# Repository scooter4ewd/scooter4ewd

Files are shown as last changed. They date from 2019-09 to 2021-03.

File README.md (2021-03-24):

# Scooter4EWD 
**Scooter 4 electric wheel drive** - электрическое транспортного средства с четырьмя мотор колесами, на одну персону, созданное из доступных материалов.

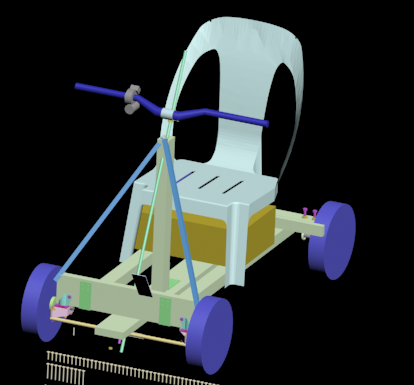
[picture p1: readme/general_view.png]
Общий вид


## Перед началом
Все ниже описанное является собственным опытом и должно расцениваться как хобби, при попытке повторить вы должны оценить как материальные затраты > 30 000 рублей, так и временные ресурсы.

## Список деталей

| №  | Деталь | шт | Цена | Сумма |
| --- | --- | ---| --- | --- |
| [1](readme/part/01/01part.md) | [Колесо гироскутера](readme/part/01/01part.md) | 4 | | 15000 (цена за 2 гироскутера) |
| [2](readme/part/02/02part.md) | [Брус 25х100х1250 (центральный лонжерон)](readme/part/02/02part.md) | 1 | | 100 |
| [3](readme/part/03/03part.md) | [Брус 25х100х500 (передняя ось)](readme/part/03/03part.md) | 1 | | |
| [4](readme/part/04/04part.md) | [Брус 40х50х960 (боковой лонжерон)](readme/part/04/04part.md) | 2 | | 150 |
| [5](readme/part/05/05part.md) | [Брус 40х50х480 (задняя ось)](readme/part/05/05part.md) | 1 | | |
| [6](readme/part/06/06part.md) | [Брус 40х50х407 (стойка рулевой колонки)](readme/part/06/06part.md) | 1 | | |
| [8](readme/part/08/08part.md) | [Уголок 40х40](readme/part/08/08part.md) | 2 | 10 | 20 |
| [9](readme/part/09/09part.md) | [Уголок 40х95](readme/part/09/09part.md) | 3 | 20 | 60 |
| [10](readme/part/10/10part.md) | [Пластина 35х100](readme/part/10/10part.md)| 4 | 10 | 40 |
| [11](readme/part/11/11part.md) | [Рым гайка м8](readme/part/11/11part.md)| 4 | 70 | 280 |
| [12](readme/part/12/12part.md) | [Болт м8х80](readme/part/12/12part.md)| 4 | 15 | 60 |
| [13](readme/part/13/13part.md) | [Болт м8х50](readme/part/13/13part.md)| 1 | 10 | 10 |
| [14](readme/part/14/14part.md) | [Гайка м8х24](readme/part/14/14part.md)| 1 | 30 | 30 |
| [15](readme/part/15/15part.md) | [Гайка м8](readme/part/15/15part.md)| 5 | 10 | 50 |
| [16](readme/part/16/16part.md) | [Шайба м8](readme/part/16/16part.md)| 4 | 5 | 20 |
| [17](readme/part/17/17part.md) | [Болт м6х40](readme/part/17/17part.md)| 10 | 10 | 100 |
| [18](readme/part/18/18part.md) | [Гайка м6](readme/part/18/18part.md)| 11 | | 50 |
| [19](readme/part/19/19part.md) | [Шайба м6](readme/part/19/19part.md)| 8 | | 40 |
| [20](readme/part/20/20part.md) | [Колесо мебельное 43х58 d40](readme/part/20/20part.md)| 2 | | 300 |
| [21](readme/part/21/21part.md) | [Болт м5х50](readme/part/21/21part.md)| 2 | | 30 |
| [22](readme/part/22/22part.md) | [Гайка м5](readme/part/22/22part.md)| 4 | | 20 |
| [23](readme/part/23/23part.md) | [Шайба м5](readme/part/23/23part.md)| 2 | | 10 |
| [24](readme/part/24/24part.md) | [Ось руля 20х20х1000](readme/part/24/24part.md)| 1 | | 75 |
| [27](readme/part/27/27part.md) | [Трубка алюминиевая d12х480](readme/part/27/27part.md)| 1 | | 50 |
| [28](readme/part/28part.md) | [Пластина 25х60](readme/part/28part.md)| 1 | | 20 |
| [29](readme/part/29/29part.md) | [Вынос руля](readme/part/29/29part.md)| 1 | | 25 |
| [30](readme/part/30/30part.md) | [Уголок алюминиевый 15х580](readme/part/30/30part.md)| 2 | | 100 |
| [31](readme/part/31part.md) | [Стул пластмассовый](readme/part/31part.md)| 1 | | 300 |
| [32](readme/part/32/32part.md) | [Руль велосипедный](readme/part/32/32part.md)| 1 | | 600 |
| [33](readme/part/33part.md) | [Ручка газа](readme/part/33part.md)| 1 | | 460 |
| [34](readme/part/34/34part.md) | [Саморез 25](readme/part/34/34part.md)| 59 | | 100 |
| [35](readme/part/35/35part.md) | [Саморез 50](readme/part/35/35part.md)| 10 | | 20 |
| [36](readme/part/36/36part.md) | [Стяжка 3х200](readme/part/36/36part.md)| 17 | | 150 |
| [38](readme/part/38/38part.md) | [Чемодан](readme/part/38/38part.md)| 1 | | 1500 |
| [39](readme/part/39/39part.md) | [Разъем DHS-78](readme/part/39/39part.md)| 1 | | 400 |
| [40](readme/part/40part.md) | [Провод силовой](readme/part/40part.md)| 10 | | 500 |
| [41](readme/part/41part.md) | [Витая пара](readme/part/41part.md)| 10 | | 200 |
| [42](readme/part/42part.md) | [Рукав металлический](readme/part/42part.md)| 1 | | 50 |
| [43](readme/part/43part.md) | [Клеммная колодка](readme/part/43part.md)| 4 | | 50 |
| [52](readme/part/52/52part.md) | [Поворотный механизм - кулак левый](readme/part/52/52part.md)| 1 | | 300 |
| [53](readme/part/53/53part.md) | [Поворотный механизм - кулак правый](readme/part/53/53part.md)| 1 | | 300 |
| [54](readme/part/54/54part.md) | [Втулка оси руля (низ)](readme/part/54/54part.md)| 1 | | 300 |
| [55](readme/part/55/55part.md) | [Подшипник руля (болт)](readme/part/55/55part.md)| 2 | | 300 |
| [56](readme/part/56/56part.md) | [Подшипник руля (гайка)](readme/part/56/56part.md)| 2 | | 300 |
| [57](readme/part/57/57part.md) | [Втулка оси руля (верх)](readme/part/57/57part.md)| 1 | | 300 |
| [58](readme/part/58part.md) | [Аккумулятор](readme/part/58part.md)| 2 | 1950 | 3900 |
| [59](readme/part/59part.md) | [Контроллер электродвигателя 350wt](readme/part/59part.md)| 4 | 600 | 2400 |
| [60](readme/part/60part.md) | [Зарядное устройство от гироскутера](readme/part/60part.md)| 1 | | |
| [61](readme/part/61part.md) | [Автомат защиты](readme/part/61part.md)| 2 | 150 | 300 |
| [62](readme/part/62part.md) | [Ваттметр](readme/part/62part.md)| 1 | 700 | 700 |
| [63](readme/part/63part.md) | [Кнопка заднего хода](readme/part/63part.md)| 1 | 70 | 70 |
| [64](readme/part/64part.md) | [Кнопка нажатия тормоза](readme/part/64part.md)| 1 | 50 | 50 |
| [65](readme/part/65part.md) | [Блок кнопок на руль](readme/part/65part.md)| 1 | 200 | 200 |
| [66](readme/part/66part.md) | [Грипсы](readme/part/66part.md)| 2 | | 300 |
| [67](readme/part/67/67part.md) | [Ротор дискового тормоза](readme/part/67/67part.md)| 2 | | |
| [68](readme/part/68part.md) | [Суппорт дискового тормоза](readme/part/68part.md)| 2 | | 2500 |
| [69](readme/part/69part.md) | [Гидролиния](readme/part/69part.md)| 2 | | |
| [70](readme/part/70part.md) | [Ручка тормоза](readme/part/70part.md)| 2 | | |
| [71](readme/part/71/71part.md) | [Проставка для ротора дискового тормоза](readme/part/71/71part.md)| 2 | | 300 |
| [72](readme/part/72part.md) | [Тумблер](readme/part/72part.md)| 8 | | 400 |
| [73](readme/part/73part.md) | [Разъем XT60 папа](readme/part/73part.md)| 8 | | 400 |
| [74](readme/part/74part.md) | [Консоль включения аккумуляторов](readme/part/74part.md)| 1 | | |
| [75](readme/part/75part.md) | [Крепление суппорта дискового тормоза](readme/part/75part.md)| 2 | | 100 |
| [76](readme/part/76part.md) | [Тяга рулевого управления](readme/part/76part.md)| 2 | | 1000 |
| | | | **итого** | **35390** |

## Как строить
1. Брус 25х100 нарезать по длине на 1250мм и 500мм, получаем детали центральный лонжерон ([№2](readme/part/02/02part.md)), 
передняя ось ([№3](readme/part/03/03part.md)).
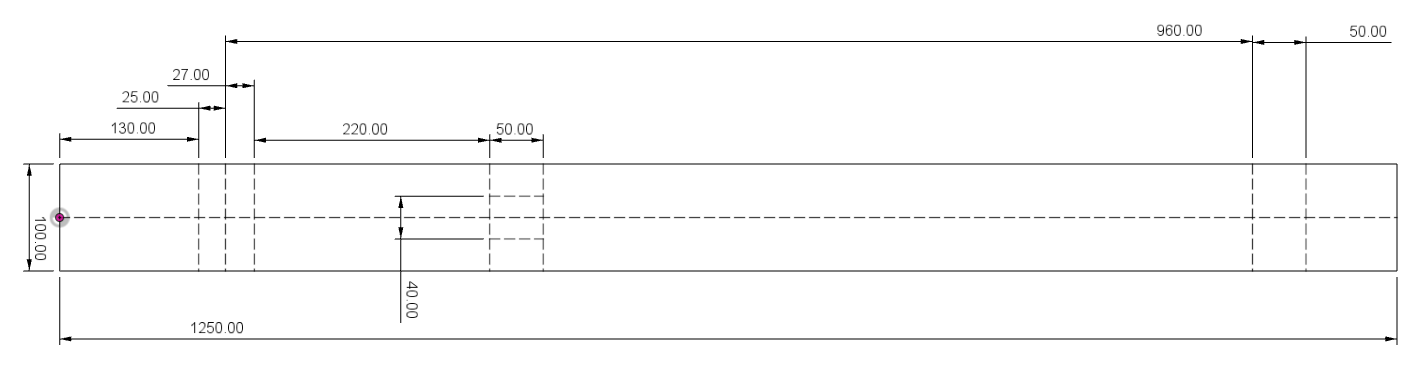
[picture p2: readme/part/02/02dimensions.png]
1. Наносим разметку на центральный лонжерон ([№2](readme/part/02/02part.md)). 
   1. Линию вдоль доски - центральную ось (50мм от бока).
   1. Место крепления передней оси ([№3](readme/part/03/03part.md)): перпендикулярная линия 130мм от края и 
   еще одну через 25мм (155мм от края).
   1. Место крепления стойки руля ([№6](readme/part/06/06part.md)): перпендикулярная линия 375мм от края, 
   еще одну через 50мм (425мм от края), 
   нарисовать прямоугольник 50х40мм на основе полученных ранее линий и по центру по ширине (20мм от оси).
   1. Место крепления задней оси ([№5](readme/part/05/05part.md)): перпендикулярная линия 1115мм от края, 
   еще одну через 50мм (1165мм от края). 
1. Просверлить отверстие для руля ([№24](readme/part/24/24part.md)), диаметр 30мм, на расстоянии 27мм от передней оси (182мм от края), отверстие должно идти под углом 22,5° (его можно получить если из листа А4 вырезать прямоугольный треугольник со сторонами 297мм на 123мм).
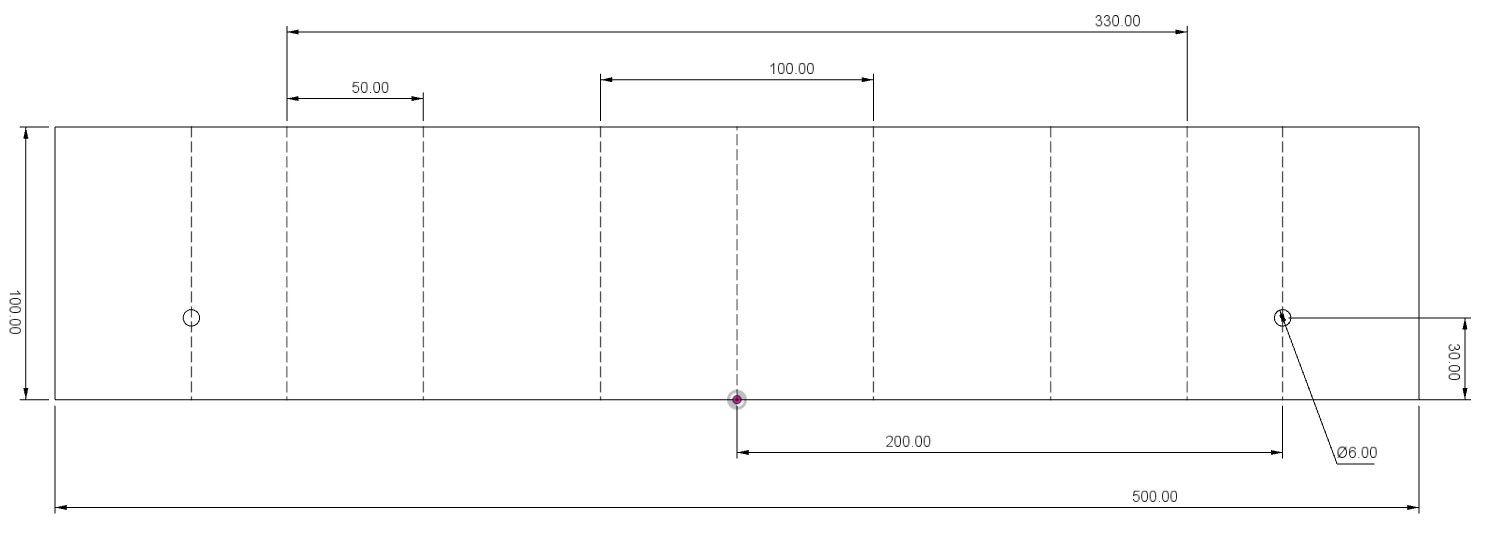
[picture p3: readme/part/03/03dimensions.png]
1. Наносим разметку на переднюю ось ([№3](readme/part/03/03part.md)). 
   1. Линию оси (250мм от края).
   1. Линии центрального лонжерона 50мм в обе стороны от ось.
   1. Линии боковых лонжеронов 115мм и 165мм по обе стороны от ось.
   1. Линии крепления передних колес 200мм по обе стороны от ось.
   1. Центр отверстия крепления механизма вращения передних колес, на линии из предыдущего пункта на расстоянии 30мм от бока.
1. Просверлить отверстия диаметром 6мм для крепления механизма вращения передних колес ([№20](readme/part/20/20part.md)
1. Брус 40х50 нарезать по длине на 960мм два штуки, 480мм, 407мм, получаем детали боковые лонжероны ([№4](readme/part/04/04part.md)), 
задняя ось ([№5](readme/part/05/05part.md)), стойка рулевой колонки ([№6](readme/part/06/06part.md)))
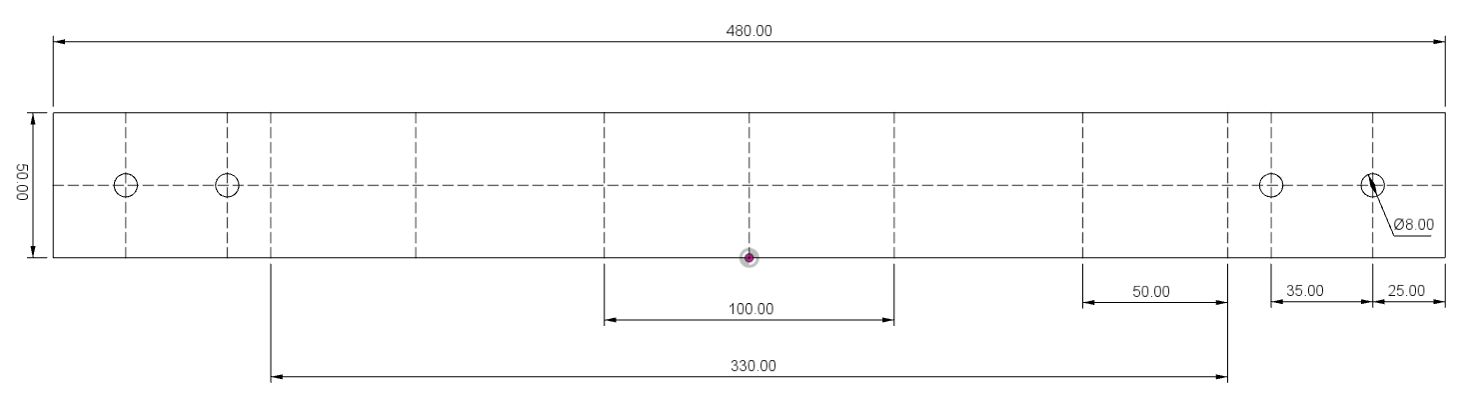
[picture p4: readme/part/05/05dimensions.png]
1. Наносим разметку на заднюю ось ([№5](readme/part/05/05part.md)) 
   1. Линию оси вдоль (25мм от бока).
   1. Линию оси по ширите (240мм от края).
   1. Линии центрального лонжерона 50мм в обе стороны от ось.
   1. Линии боковых лонжеронов 115мм и 165мм по обе стороны от ось.
   1. Линии крепления задних колес 25мм и 60мм по обе стороны от края.
1. Просверлить отверстия диаметром 8мм для крепления задних колес.
1. Собираем основу рамы, на ровной поверхности выкладываем прямоугольник из передней оси ([№3](readme/part/03/03part.md)), 
лонжероны 2 шт ([№4](readme/part/04/04part.md)), задняя ось ([№5](readme/part/05/05part.md)), проверяем что углы прямые
1. Полученный прямоугольник соединяем, заднюю ось ([№5](readme/part/05/05part.md)) уголками ([№8](readme/part/08big.md) по внутреннему периметру двенадцатью саморезами ([№34](readme/part/34/34part.md)),
1. Переднюю ось ([№3](readme/part/03/03part.md)) уголком ([№9](readme/part/09/09part.md)). 
Уголок необходимо подложить под раму, сначала крепим уголок к передней оси восьмью саморезами ([№34](readme/part/34/34part.md)), 
затем подымаем раму и фиксируем уголки на боковых лонжеронах 8 саморезами ([№35](readme/part/35/35part.md)).
1. Усиливаем крепление задней оси прикручивая пластина 35х100 ([№10](readme/part/10/10part.md)) 12 саморезами ([№34](readme/part/34/34part.md))
1. Выставляем по центру лонжерон ([№2](readme/part/02/02part.md)), прикручиваем 6 саморезами ([№35](readme/part/35/35part.md)), 
три к передней оси ([№3](readme/part/03/03part.md)), три к задней оси ([№5](readme/part/05/05part.md)) 
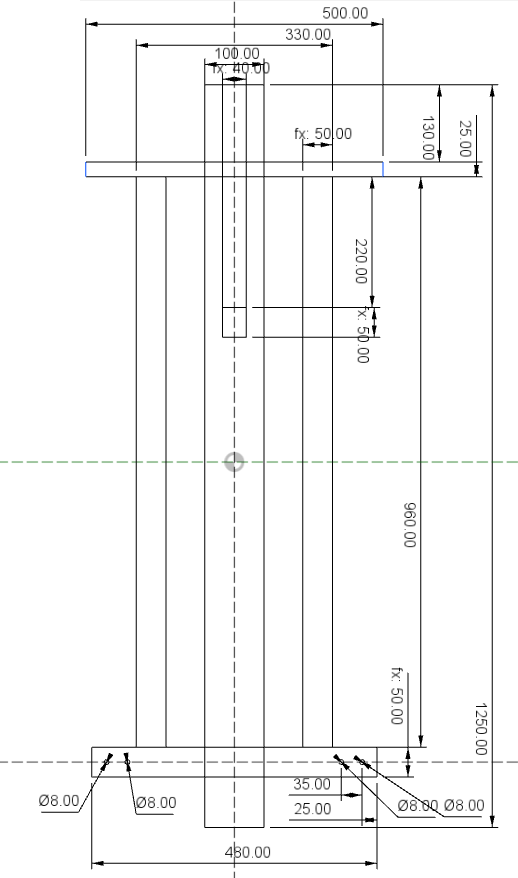
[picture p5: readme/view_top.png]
Общий чертёж

1. На четыре болта ([№12](readme/part/12/12part.md)) накрутить четыре гайки (№15) и надеть четыре шайбы ([№16](readme/part/16/16part.md).
1. Болты ([№12](readme/part/12/12part.md)) вставить в заднюю ось ([№5](readme/part/05/05part.md)), 
наживить рым гайками ([№11](readme/part/11/11part.md)). 
1. Пара рым гайками ([№11](readme/part/11/11part.md)) с одной стороны должна держать ось колеса ([№1](readme/part/01/01part.md)).
   1. Прижать ось колеса ([№1](readme/part/01/01part.md)) болтом ([№12](readme/part/12/12part.md)).
   1. Зафиксировать болт ([№12](readme/part/12/12part.md)) на оси подтянув гайку ([№11](readme/part/11/11part.md)).
1. Необходимо добиться параллельности оси колес ([№1](readme/part/01/01part.md)) к задней оси ([№5](readme/part/05/05part.md)). 
Проверить под нагрузкой - стать на заднюю ось ([№5](readme/part/05/05part.md)). 
В случае необходимости, рым гайками ([№11](readme/part/11/11part.md)), можно подпилить напильником.
1. Мебельное колесо ([№20](readme/part/20/20part.md)) разобрать, вынуть колесо.
1. Мебельное колесо ([№20](readme/part/20/20part.md)) крепим к передней оси за ухо в котором было колесико.
1. В поворотный кулак ([№52](readme/part/52/52part.md)) вставить ось колеса ([№1](readme/part/01/01part.md)).
1. Поворотный кулак ([№52](readme/part/52/52part.md)) вместе с колесом ([№1](readme/part/01/01part.md)) 
крепим к площадке мебельного колеса ([№20](readme/part/20/20part.md)) четырьмя болтами ([№17](readme/part/17/17part.md)), 
подкладываем шайбы  ([№19](readme/part/19/19part.md)), закручиваем гайку ([№18](readme/part/18/18part.md))
1. Аналогично с другой стороны для ([№53](readme/part/53/53part.md))
1. Поворотные кулаки ([№52](readme/part/52/52part.md), [№53](readme/part/53/53part.md)) между собой соединяем трубкой ([№27](readme/part/27/27part.md)).
Для этого нам понадобится два болта ([№21](readme/part/21/21part.md)), две шайбы ([№23](readme/part/21/21part.md)) и шесть гаек ([№22](readme/part/22/22part.md))
   1. В трубке ([№27](readme/part/27/27part.md)) просверлить отверстие диаметром 5мм в 5мм от края. Расстояние между отверстиями должно составлять 480мм.
   1. Болт ([№21](readme/part/21/21part.md)) продеть в отверстие в трубке ([№27](readme/part/27/27part.md)).
   1. Наживить гайку ([№22](readme/part/22/22part.md)) вплотную к трубке ([№27](readme/part/27/27part.md)).
   1. Смазать болт ([№21](readme/part/21/21part.md)), можно использовать обычное мыло, этого будет достаточно.
   1. Болт ([№21](readme/part/21/21part.md)) вкрутить в поворотный кулак ([№52](readme/part/52/52part.md)).
   1. Затянуть гайку ([№22](readme/part/22/22part.md)) зафиксировав болт ([№21](readme/part/21/21part.md)) на трубке.
   1. Надеть шайбу ([№23](readme/part/21/21part.md)).
   1. Наживить гайку ([№22](readme/part/22/22part.md)) вплотную к шайбе ([№23](readme/part/21/21part.md)).
   1. Наживить еще одну гайку ([№22](readme/part/22/22part.md)) вплотную к предыдущей.
   1. Затянуть гайки между собой, болт ([№21](readme/part/21/21part.md)) должен свободно вращаться в кулаке ([№52](readme/part/52/52part.md)).
1. Повторить процедуру с другой стороны
1. К стойку руля ([№6](readme/part/06/06part.md)) к краю крепим уголок ([№9](readme/part/09/09part.md)) на четыре самореза ([№34](readme/part/34/34part.md))
1. Вторую площадку уголка ([№9](readme/part/09/09part.md)) крепим к центральному лонжерону ([№2](readme/part/02/02part.md)) на четыре самореза ([№34](readme/part/34/34part.md)), 
выставив брус ([№6](readme/part/06/06part.md)) перпендикулярно на размеченный в центре прямоугольник.
1. Нижняя втулка руля ([54](readme/part/54/54part.md)) крепится двумя саморезами ([№35](readme/part/35/35part.md)) к передней оси ([№3](readme/part/03/03part.md))
и двумя саморезами ([№35](readme/part/35/35part.md)) к центральному лонжерону ([№2](readme/part/02/02part.md)).
1. Верхняя втулка руля ([57](readme/part/57/57part.md)) крепится к стойке рулевой колонки ([6](readme/part/06/06part.md)) 
двумя пластинами ([10](readme/part/10/10part.md)) с боков на шестнадцать саморезов ([№34](readme/part/34/34part.md)) 
1. Для увеличение жесткости стойки руля, два уголка ([30](readme/part/30/30part.md)) крепим к верхней втулке руля ([57](readme/part/57/57part.md))
с одной стороны и к краю передней оси ([3](readme/part/03/03part.md)) с другой стороны.
1. TODO Ось руля ([24](readme/part/24/24part.md)) 
1. TODO Вынос руля ([29](readme/part/29/29part.md)), руль ([24](readme/part/24/24part.md))
1. TODO Стул ([31](readme/part/31part.md))
1. TODO Педаль тормоза Петля ввертная ([49](readme/part/49part.md)) Алюминиевый профиль ([50](readme/part/50part.md)) Брус 16х51х150
1. TODO Трос тормоза
1. TODO Уголок крепления блока тормоза
1. TODO Блок тормоза 1
1. TODO Блок тормоза 2
1. TODO Трос
1. TODO Чемодан
1. TODO Аккумулятор
1. TODO Клеммы аккумуляторов
1. TODO Автомат
1. TODO Клеммы питания
1. TODO Контроллеры
1. TODO Клеммы перед разъемом
1. TODO Разъем
1. TODO Клеммы переднего левого колеса
1. TODO Клеммы переднего правого колеса
1. TODO Провода от передних клем до разъема
1. TODO Провода от ручки газа до разъема
1. TODO Клеммы заднего левого колеса
1. TODO Клеммы заднего правого колеса
1. TODO Провода от задних клем до разъема
1. TODO Стяжки изолента

[Распайка разъема](readme/part/39/39part.md)

## Замечания и рекомендации
Мебельные колёса для крепления передних колес необходимо выбирать с запасом прочности и наличием подшипников с двух сторон.

При распайке разъема использовать все пины даже если они не задействованы, 
припаять провод и оставить на нем бирку поможет в дальнейших изменениях (после установки впаять дополнительный провод нереально).

Перед подачей питания, прозвонить каждый провод на обрыв и замыкания между собой.

## Лирика 
Раздел не несет технической информации, но может внести ясность почему так получилось. 
[Читать далее->](readme/history.md)

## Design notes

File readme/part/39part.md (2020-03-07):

# Разем DHS-78

Разем DHS-78

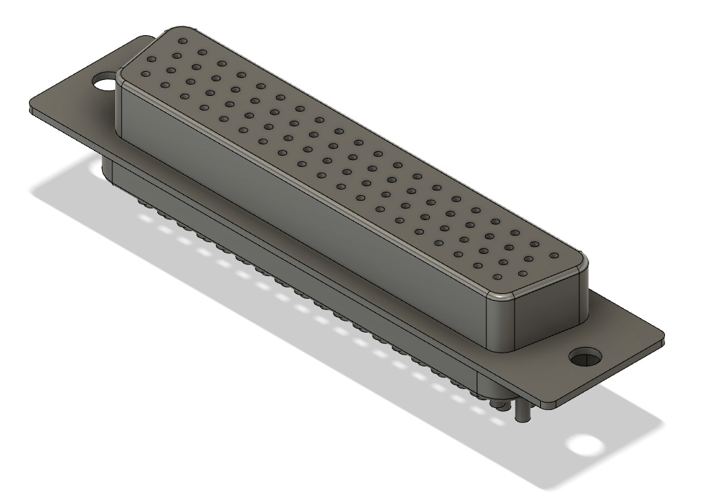
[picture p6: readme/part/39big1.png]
Мама

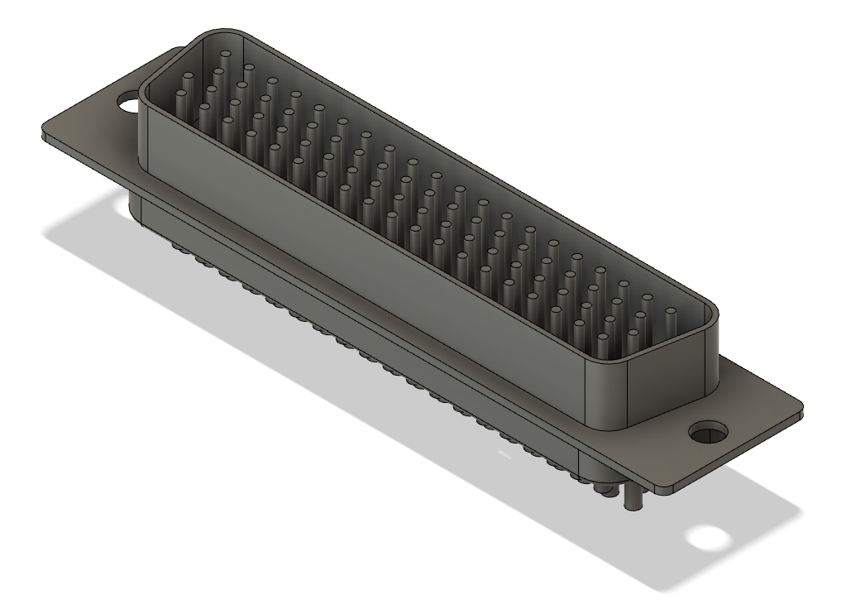
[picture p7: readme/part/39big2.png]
Папа


## Распайка разъема

| № Pin | Ряд | Обозначение | Расшифровка |
| --- | --- | --- | --- |
| 1  | 1 | кппж | колесо передний правый желтый |
| 2  | 1 | кппж |  |
| 3  | 1 | кппз | колесо передний правый зеленый |
| 4  | 1 | кппз |  |
| 5  | 1 | кппс | колесо передний правый синий |
| 6  | 1 | кппс |  |
| 7  | 1 | кплж | колесо передний левый желтый |
| 8  | 1 | кплж |  |
| 9  | 1 | кплз | колесо передний левый зеленый |
| 10 | 1 | кплз |  |
| 11 | 1 | кплс | колесо передний левый синий |
| 12 | 1 | кплс |  |
| 13 | 1 | s+36 | speed +36v (от аккумулятора) |
| 14 | 1 | s вкл | speed вкл. контроллера (замыкается на провод +36v) |
| 15 | 1 | задний ход 1 | задний ход 1 TODO (земля) |
| 16 | 1 | speed | speed уровень газа (+1v .. +4v) |
| 17 | 1 | задний ход 2 | задний ход 2 TODO (замыкается за землю) |
| 18 | 1 | s+5 | speed +5v |
| 19 | 1 | хп+5 | холла передний +5v |
| 20 | 1 | хз+5 | холла задний +5v |
| 21 | 2 | кппж |  |
| 22 | 2 | кппж |  |
| 23 | 2 | кппз |  |
| 24 | 2 | кппз |  |
| 25 | 2 | кппс |  |
| 26 | 2 | кппс |  |
| 27 | 2 | кплж |  |
| 28 | 2 | кплж |  |
| 29 | 2 | кплз |  |
| 30 | 2 | кплз |  |
| 31 | 2 | кплс |  |
| 32 | 2 | кплс |  |
| 33 | 2 | хппж | холла передний правый желтый |
| 34 | 2 | хппз | холла передний правый зеленый |
| 35 | 2 | хппс | холла передний правый синий |
| 36 | 2 | хплж | холла передний левый желтый |
| 37 | 2 | хплз | холла передний левый зеленый |
| 38 | 2 | хплс | холла передний левый синий |
| 39 | 2 |  |  |
| 40 | 3 | кзпж | колесо задний правый желтый |
| 41 | 3 | кзпж |  |
| 42 | 3 | кзпз | колесо задний правый зеленый |
| 43 | 3 | кзпз |  |
| 44 | 3 | кзпс | колесо задний правый синий |
| 45 | 3 | кзпс |  |
| 46 | 3 | кзлж | колесо задний левый желтый |
| 47 | 3 | кзлж |  |
| 48 | 3 | кзлз | колесо задний левый зеленый |
| 49 | 3 | кзлз |  |
| 50 | 3 | кзлс | колесо задний левый синий |
| 51 | 3 | кзлс |  |
| 52 | 3 | хзпж | холла задний правый желтый |
| 53 | 3 | хзпз | холла задний правый зеленый |
| 54 | 3 | хзпс | холла задний правый синий |
| 55 | 3 | хзлж | холла задний левый желтый |
| 56 | 3 | хзлз | холла задний левый зеленый |
| 57 | 3 | хзлс | холла задний левый синий |
| 58 | 3 |  |  |
| 59 | 3 |  |  |
| 60 | 4 | кзпж |  |
| 61 | 4 | кзпж |  |
| 62 | 4 | кзпз |  |
| 63 | 4 | кзпз |  |
| 64 | 4 | кзпс |  |
| 65 | 4 | кзпс |  |
| 66 | 4 | кзлж |  |
| 67 | 4 | кзлж |  |
| 68 | 4 | кзлз |  |
| 69 | 4 | кзлз |  |
| 70 | 4 | кзлс |  |
| 71 | 4 | кзлс |  |
| 72 | 4 |  |  |
| 73 | 4 |  |  |
| 74 | 4 | s- | speed минус (земля) |
| 75 | 4 | хп- | холла передний минус (земля) |
| 76 | 4 | хз- | холла задний минус (земля) |
| 77 | 4 |  |  |
| 78 | 4 |  |  |

Силовые провода к колесам используют по 4 пина, имеют одинаковое обозначение и расположены рядом - два на одном ряду и два на соседнем.

## 3D модели
- [Папа](39_1part.f3d)
- [Мама](39_2part.f3d)

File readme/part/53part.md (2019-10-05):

# Поворотный механизм - кулак правый

Поворотный механизм - кулак правый.
Файлы от левого кулака перед использованием сделать зеркальную копию.

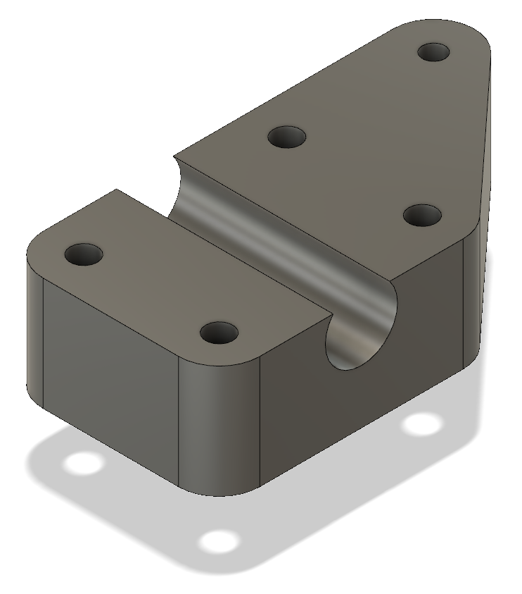
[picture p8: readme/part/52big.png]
Общий вид


[3D модель](52part.f3d)

[Файл для печати на 3D принтере](52part.stl)

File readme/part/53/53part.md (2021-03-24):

# Поворотный механизм - кулак правый

Поворотный механизм - кулак правый.
Файлы от левого кулака перед использованием сделать зеркальную копию.

Общий вид

[3D модель](../52/52part.f3d)

[Файл для печати на 3D принтере](../52/52part.stl)

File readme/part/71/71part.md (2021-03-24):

# Проставка для ротора дискового тормоза

Проставка для ротора дискового тормоза.

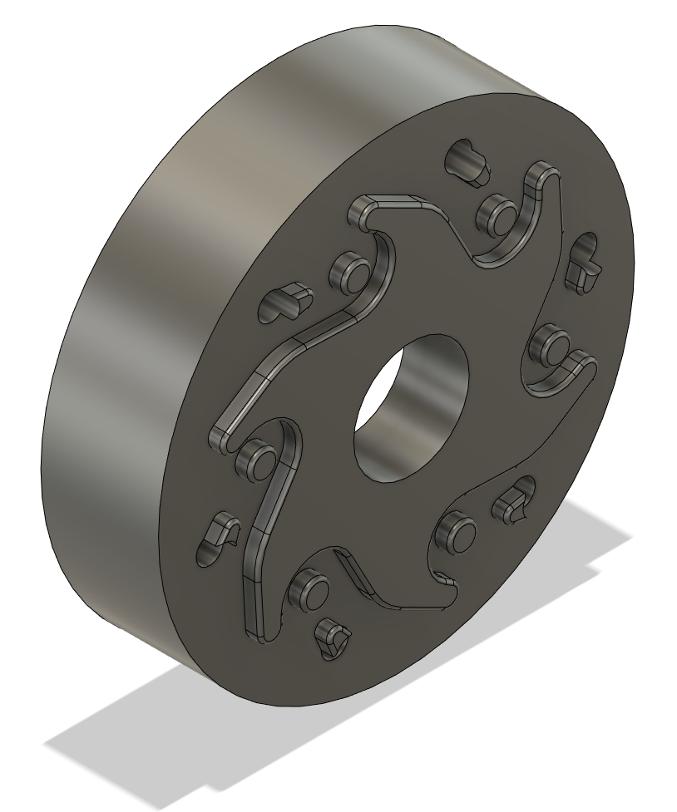
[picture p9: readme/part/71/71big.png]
Общий вид


[3D модель](71part.f3z)

[Файл для печати на 3D принтере](71part.stl)

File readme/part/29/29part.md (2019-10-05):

# Вынос руля

Вынос руля

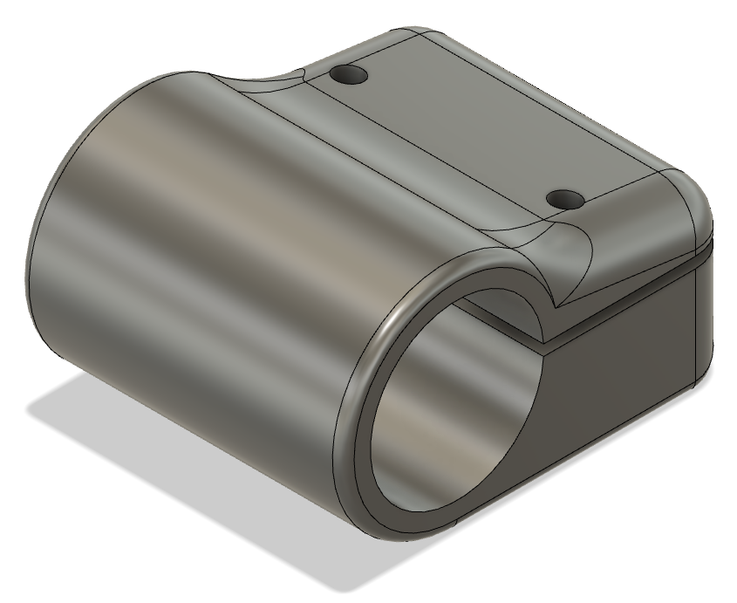
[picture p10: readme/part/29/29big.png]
Общий вид


[3D модель](29part.f3d)

Файл для печати на 3D принтере:
- [Вынос](29part.stl)

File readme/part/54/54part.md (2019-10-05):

# Втулка оси руля низ

Втулка оси руля низ

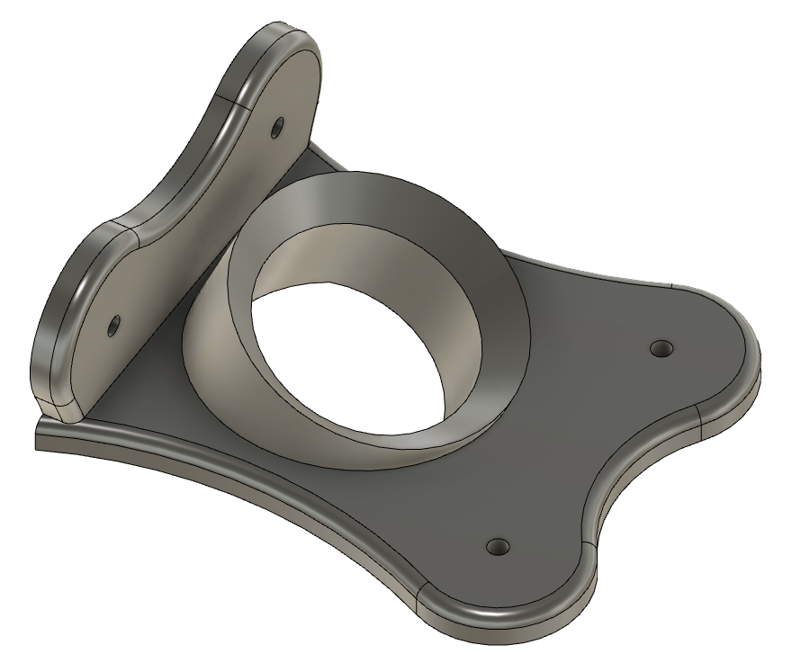
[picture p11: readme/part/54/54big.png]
Общий вид


[3D модель](54part.f3d)

[Файл для печати на 3D принтере](54part.stl)

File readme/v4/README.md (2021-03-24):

# Scooter4EWD 
**Scooter 4 electric wheel drive** - электрическое транспортного средства с четырьмя мотор колесами, на одну персону, созданное из доступных материалов.

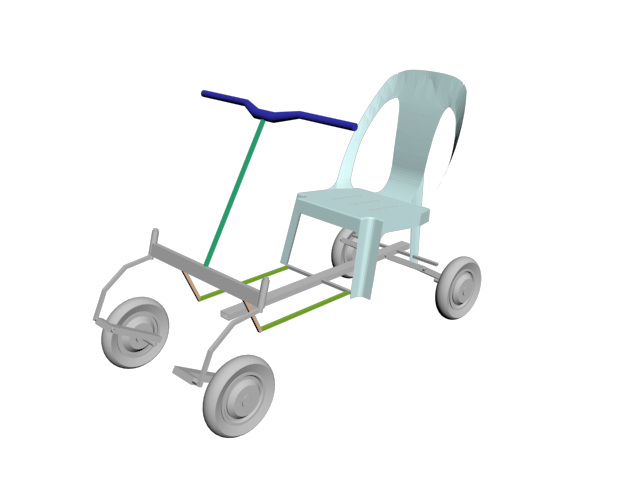
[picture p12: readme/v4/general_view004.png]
Общий вид


## Перед началом
Все ниже описанное является собственным опытом и должно расцениваться как хобби, при попытке повторить вы должны оценить как материальные затраты > 30 000 рублей, так и временные ресурсы.

## Список деталей
TODO

| №  | Деталь | шт | Цена | Сумма |
| --- | --- | ---| --- | --- |
| [1](../part/01/01part.md) | [Колесо гироскутера](../part/02/02part.md) | 4 | | 15000 (цена за 2 гироскутера) |
| [31](../part/31part.md) | [Стул пластмассовый](../part/31part.md)| 1 | | 300 |
| [32](../part/32/32part.md) | [Руль велосипедный](../part/32/32part.md)| 1 | | 600 |
| [33](../part/33part.md) | [Ручка газа](../part/33part.md)| 1 | | 460 |
| [34](../part/34/34part.md) | [Саморез 25](../part/34/34part.md)| | |  |
| [35](../part/35/35part.md) | [Саморез 50](../part/35/35part.md)|  | |  |
| [36](../part/36/36part.md) | [Стяжка 3х200](../part/36/36part.md)|  | |  |
| [38](../part/38/38part.md) | [Чемодан](../part/38/38part.md)| 1 | | 1500 |
| [39](../part/39/39part.md) | [Разъем DHS-78](../part/39/39part.md)| 1 | | 400 |
| [40](../part/40part.md) | [Провод силовой](../part/40part.md)| 10 | | |
| [41](../part/41part.md) | [Витая пара](../part/41part.md)| 10 | | |
| [42](../part/42part.md) | [Рукав металлический](../part/42part.md)| 1 | | 50 |
| [43](../part/43part.md) | [Клеммная колодка](../part/43part.md)| 4 | | 50 |
| [58](../part/58part.md) | [Аккумулятор](../part/58part.md)| 2 | 1950 | 3900 |
| [59](../part/59part.md) | [Контроллер электродвигателя 350wt](../part/59part.md)| 4 | 600 | 2400 |
| [60](../part/60part.md) | [Зарядное устройство от героскутера](../part/60part.md)| 1 | | |
| [61](../part/61part.md) | [Автомат защиты](../part/61part.md)| 1 | 150 | 150 |
| [62](../part/62part.md) | [Ваттметр](../part/62part.md)| 1 | 700 | 700 |
| [63](../part/63part.md) | [Кнопка заднего хода](../part/63part.md)| 1 | 70 | 70 |
| [64](../part/64part.md) | [Кнопка нажатия тормоза](../part/64part.md)| 1 | 50 | 50 |
| [65](../part/65part.md) | [Блок кнопок на руль](../part/65part.md)| 1 | 200 | 200 |
| [66](../part/66part.md) | [Грипсы](../part/66part.md)| 2 | | 300 |
| [67](../part/67/67part.md) | [Ротор дискового тормоза](../part/67/67part.md)| 2 | | |
| [68](../part/68part.md) | [Суппорт дискового тормоза](../part/68part.md)| 2 | | 2500 |
| [69](../part/69part.md) | [Гидролиния](../part/69part.md)| 2 | | |
| [70](../part/70part.md) | [Ручка тормоза](../part/70part.md)| 2 | | |
| [71](../part/71/71part.md) | [Проставка для ротора дискового тормоза](../part/71/71part.md)| 2 | | |
| [72](../part/72part.md) | [Тумблер](../part/72part.md)| 8 | | |
| [73](../part/73part.md) | [Разъем XT60 папа](../part/73part.md)| 8 | | |
| [74](../part/74part.md) | [Консоль включения аккумуляторов](../part/73part.md)| 1 | | |
| | | | **итого** | **** |

## Как строить
1. TODO 

[Распайка разъема](../part/39/39part.md)

## Замечания и рекомендации
TODO

## Лирика 
Раздел не несет технической информации, но может внести ясность почему так получилось. 
[Читать далее->](../history.md)

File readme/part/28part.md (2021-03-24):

# Пластина 25х60

Пластина 25х60

Общий вид

[3D модель](28part.f3d)

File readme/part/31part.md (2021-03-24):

# Стул пластмассовый

Стул пластмассовый

Общий вид

[3D модель](31part.f3d)

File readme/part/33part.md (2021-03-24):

# Ручка газа

Ручка газа, с кнопкой включения и индикацией напряжения

Общий вид

[3D модель](33part.f3d)

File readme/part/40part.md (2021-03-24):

# Провод силовой

Провод силовой 2,5мм2 многожильный.
Используются для подключения колес к чемодану и внутри чемодана от разъема до контролеров.
Три провода от каждого колеса

Общий вид

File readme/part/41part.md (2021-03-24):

# Витая пара

Витая пара

Используются для подключения:
- датчиков хола колес к разъему чемодана 
- ручки газа к разъему чемодана
- внутри чемодана от разъема до контролеров
Пять провода от каждого колеса

Общий вид

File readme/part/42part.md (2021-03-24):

# Рукав металический

Рукав металлический.

Общий вид

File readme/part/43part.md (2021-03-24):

# Клеммная колодка

Клеммная колодка

Общий вид

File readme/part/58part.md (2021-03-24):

# Аккумулятор

Аккумулятор

Общий вид

[3D модель](58part.f3d)

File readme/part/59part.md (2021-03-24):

# Контроллер электродвигателя 350wt

Контроллер электродвигателя 350wt

Общий вид

[3D модель](59part.f3d)

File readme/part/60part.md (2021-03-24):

# Зарядное устройство от гироскутера

Зарядное устройство от гироскутера 1.5A

Общий вид

[3D модель](60part.f3d)

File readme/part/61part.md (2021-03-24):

# Автомат защиты

Автомат защиты 32A

Общий вид

[3D модель](61part.f3d)

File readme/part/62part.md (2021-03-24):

# Ваттметр

Ваттметр 150A. Показывает: напряжение, ток, потребляемую мощность.

Общий вид

[3D модель](62part.f3d)

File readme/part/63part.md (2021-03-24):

# Кнопка заднего хода

Кнопка заднего хода

Общий вид

[3D модель](63part.f3d)

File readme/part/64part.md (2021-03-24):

# Кнопка нажатия тормоза

Кнопка нажатия тормоза

Общий вид

[3D модель](64part.f3d)

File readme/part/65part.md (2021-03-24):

# Блок кнопок на руль

Блок кнопок на руль. Включение света, сигнал, повороты.

Общий вид

[3D модель](65part.f3d)

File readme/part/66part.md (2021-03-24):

# Грипсы на руль

Грипсы на руль.

Общий вид

[3D модель](66part.f3d)

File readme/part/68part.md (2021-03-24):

# Суппорт дискового тормоза

Суппорт дискового тормоза.

Общий вид

[3D модель](68part.f3d)

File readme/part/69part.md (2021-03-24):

# Гидролиния

Гидролиния.

Общий вид

[3D модель](69part.f3d)

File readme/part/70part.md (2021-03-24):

# Ручка тормоза

Ручка тормоза.

Общий вид

[3D модель](70part.f3d)

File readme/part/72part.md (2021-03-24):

# Тумблер

Тумблер.

Общий вид

[3D модель](72part.f3d)

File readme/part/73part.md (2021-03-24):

# Разъем XT60 папа

Разъем XT60 папа.

Общий вид

[3D модель](73part.f3d)

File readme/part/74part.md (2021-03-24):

# Консоль включения аккумуляторов

Консоль включения аккумуляторов.

Общий вид

[3D модель](74part.f3d)

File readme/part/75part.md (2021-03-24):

# Крепление суппорта дискового тормоза

Крепление суппорта дискового тормоза.

Общий вид

[3D модель](75part.f3d)

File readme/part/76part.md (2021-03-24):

# Тяга рулевого управления

Тяга рулевого управления для квадроцикла 230мм с регулировкой по длине, с шариковым подшипником.

Общий вид

[3D модель](76part.f3d)

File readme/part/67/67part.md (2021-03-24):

# Ротор дискового тормоза

Ротор дискового тормоза

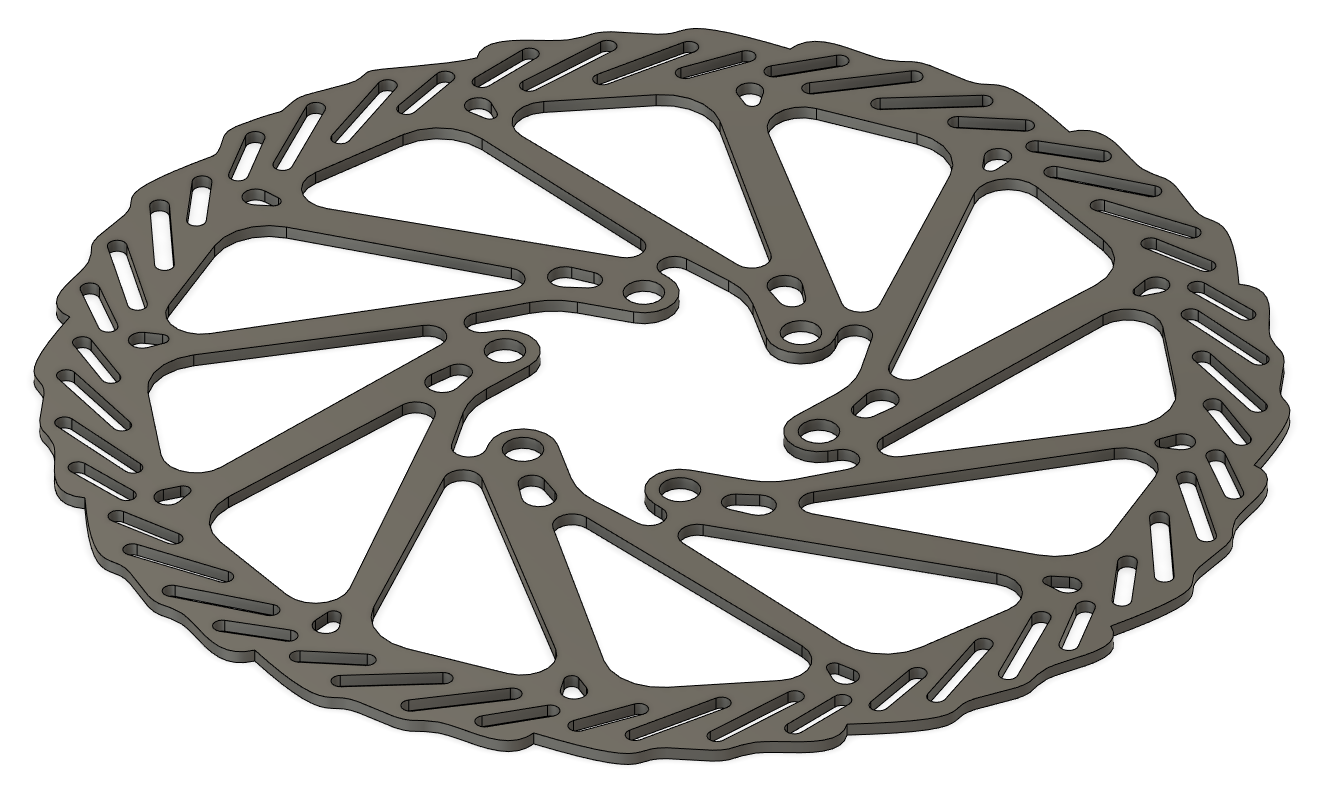
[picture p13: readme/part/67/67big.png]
Общий вид


[3D модель](67part.f3d)

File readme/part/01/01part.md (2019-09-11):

# Колесо гироскутера
Колесо гироскутера 10 дуймов

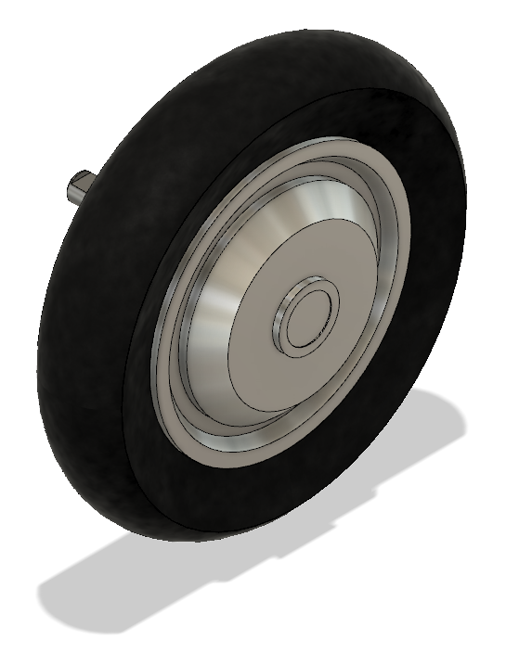
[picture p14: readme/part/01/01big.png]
Общий вид


[3D модель](01part.f3d)

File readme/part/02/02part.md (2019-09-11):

#  Центральный лонжерон

Брус 25х100х1250

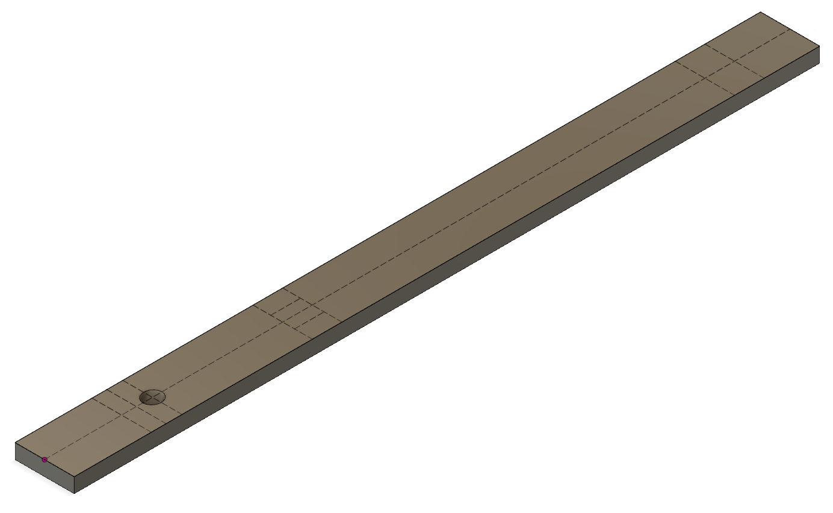
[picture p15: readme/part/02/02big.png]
Общий вид


Размеры

[3D модель](02part.f3d)

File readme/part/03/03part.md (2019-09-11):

#  Передняя ось

Брус 25х100х500

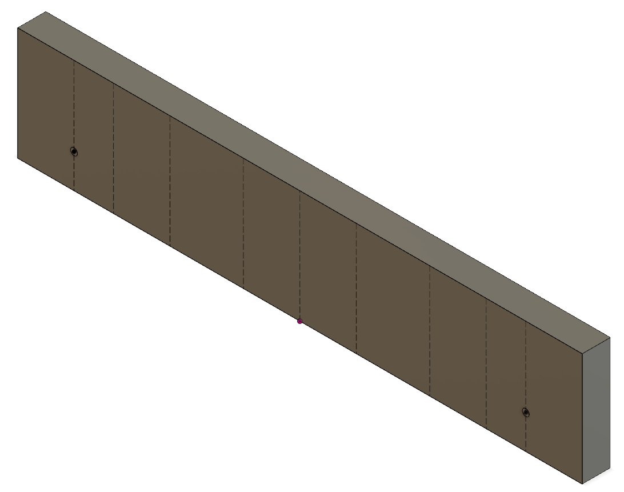
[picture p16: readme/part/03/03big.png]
Общий вид


Размеры

[3D модель](03part.f3d)

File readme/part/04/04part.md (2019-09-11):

#  Боковой лонжерон

Брус 40х50х960

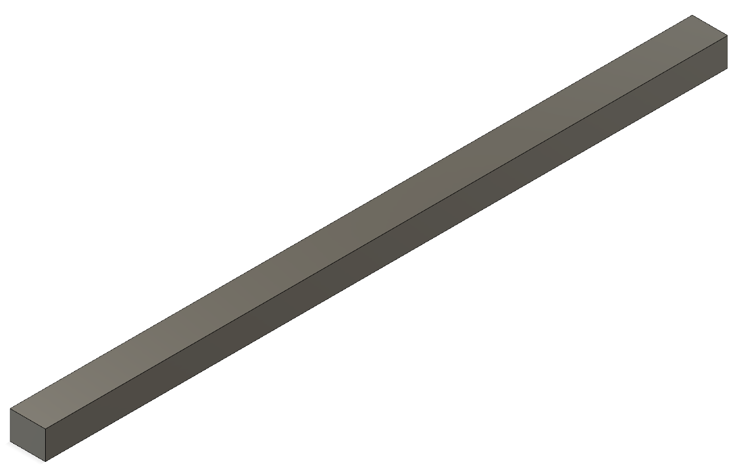
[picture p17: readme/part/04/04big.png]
Общий вид


[3D модель](04part.f3d)

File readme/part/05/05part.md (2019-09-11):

# Задняя ось

Брус 40х50х480

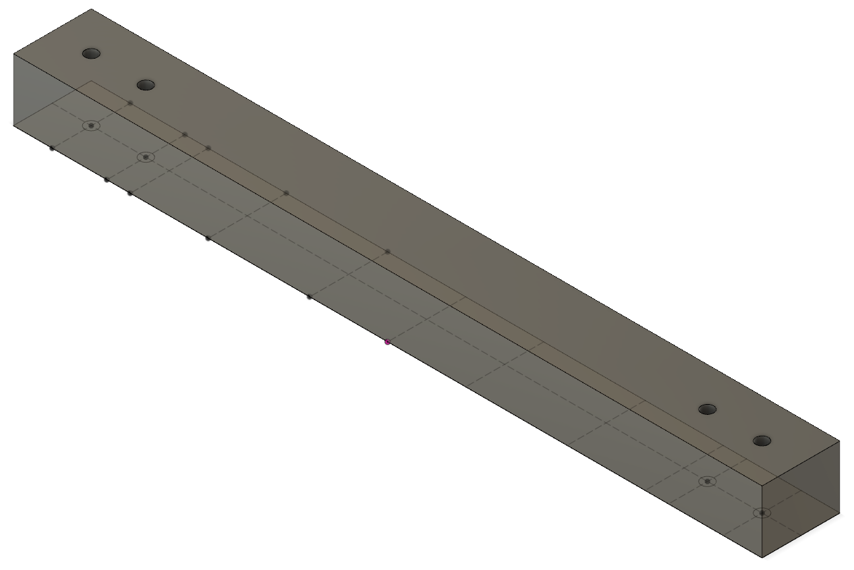
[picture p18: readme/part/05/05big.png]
Общий вид


Размеры

[3D модель](05part.f3d)

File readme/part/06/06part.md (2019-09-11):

# Стойка рулевой колонки

Брус 40х50х407

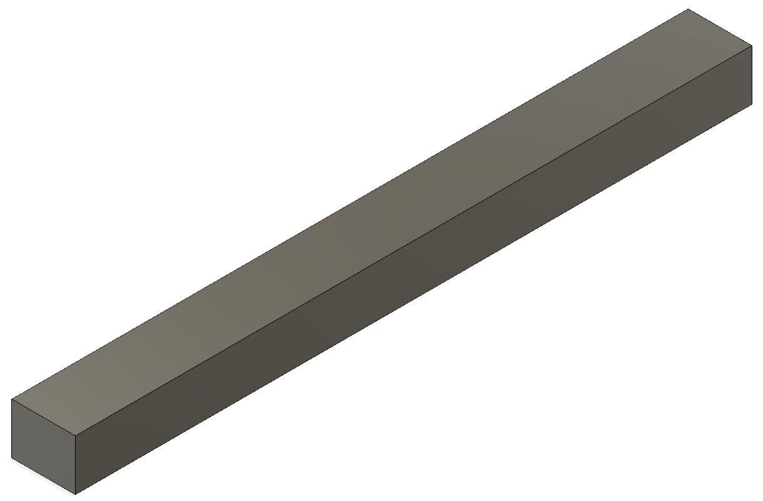
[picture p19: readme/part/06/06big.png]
Общий вид


[3D модель](06part.f3d)

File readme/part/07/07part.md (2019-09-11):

# Тормоз

Брус 18х36х600

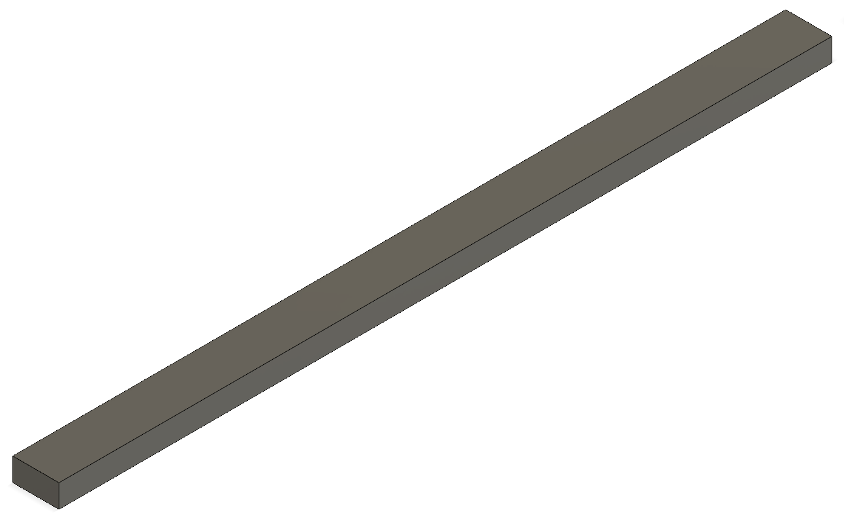
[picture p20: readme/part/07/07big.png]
Общий вид


[3D модель](07part.f3d)

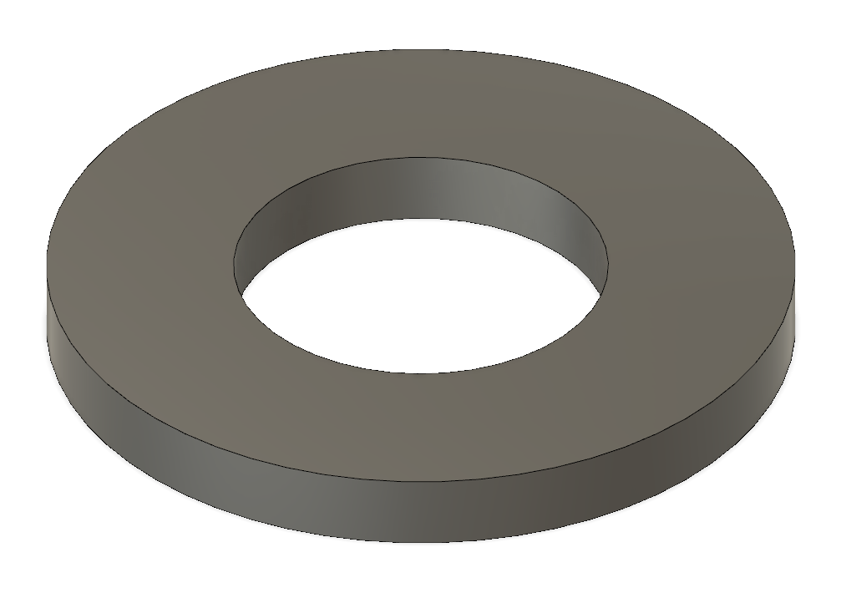
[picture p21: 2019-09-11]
readme/part/23/23big.png

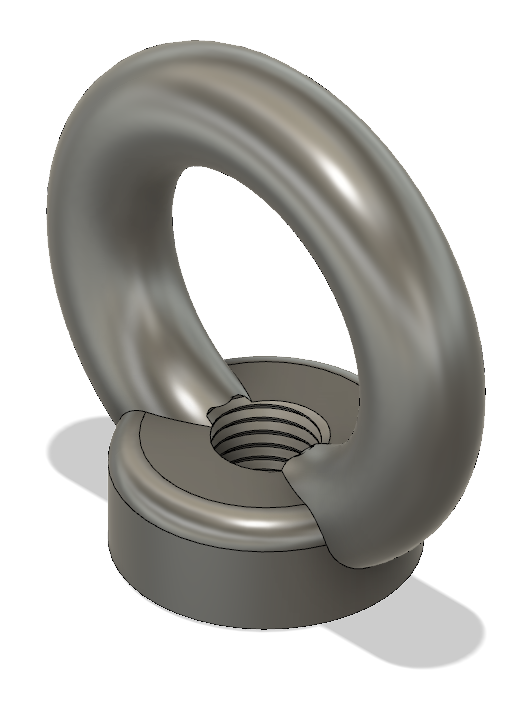
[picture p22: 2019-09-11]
readme/part/11/11big.png

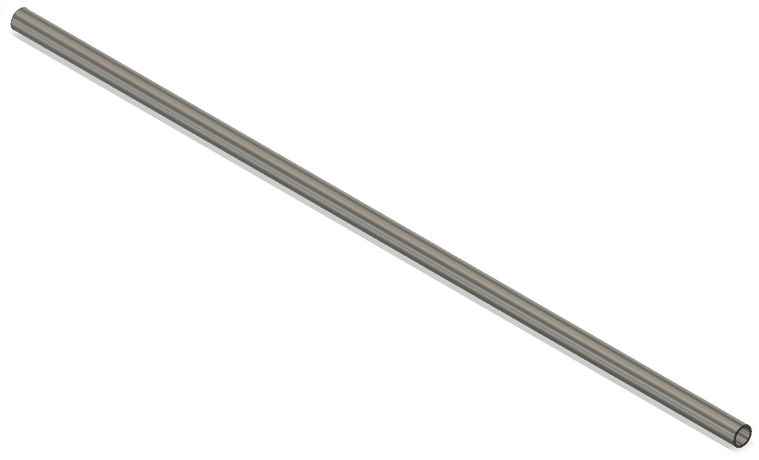
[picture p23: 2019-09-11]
readme/part/27/27big.png

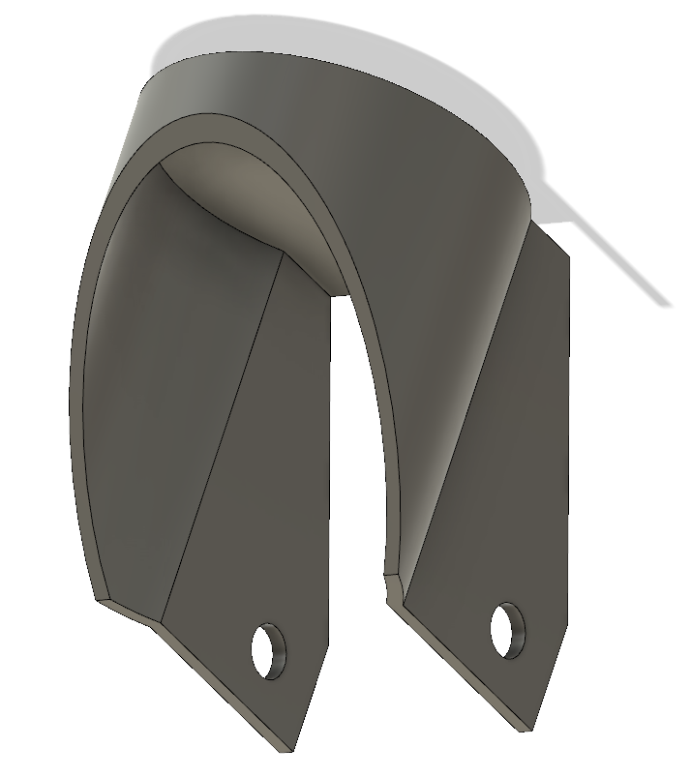
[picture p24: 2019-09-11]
readme/part/20/20big.png

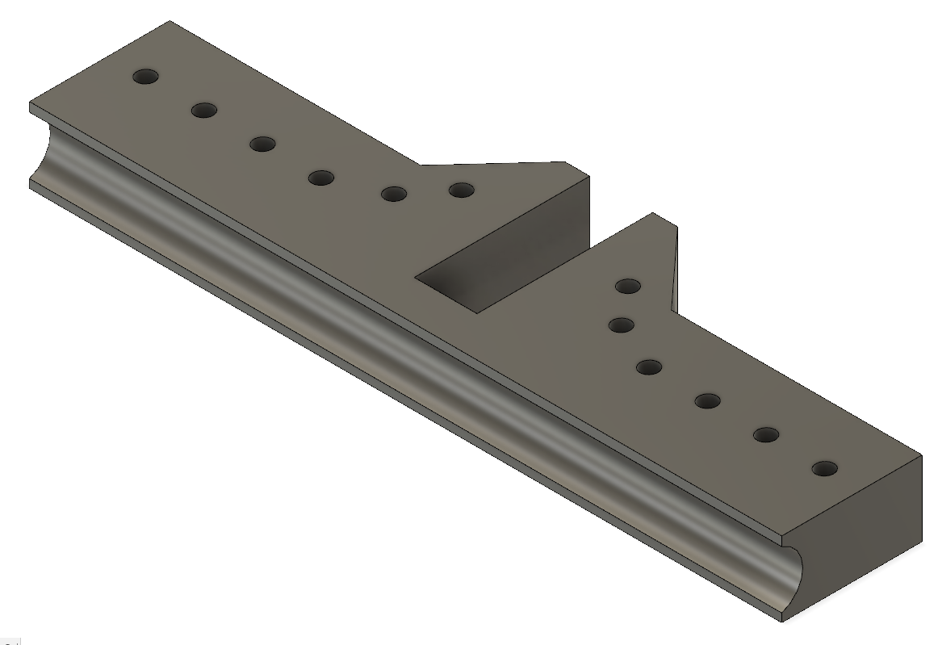
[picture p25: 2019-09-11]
readme/part/37/37big.png

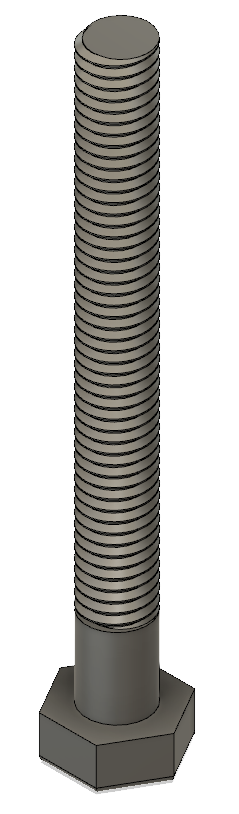
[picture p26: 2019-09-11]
readme/part/21/21big.png

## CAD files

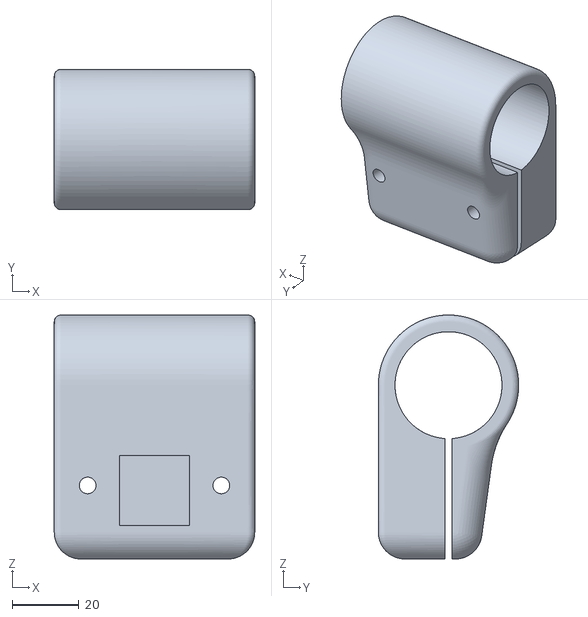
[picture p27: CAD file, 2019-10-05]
readme/part/29/29part.stl
60.0 x 42.0 x 73.0

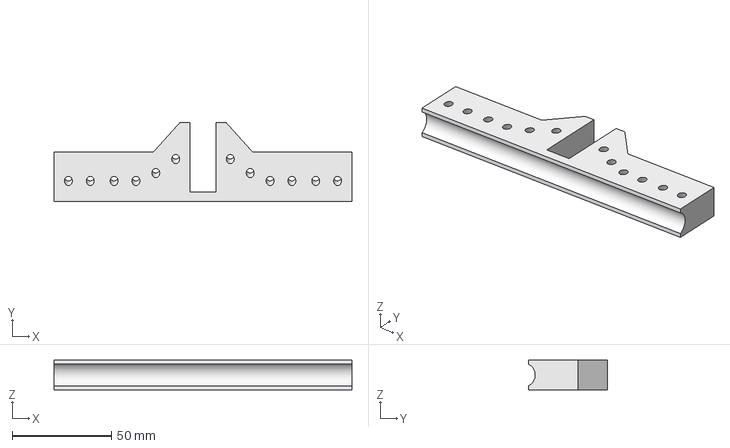
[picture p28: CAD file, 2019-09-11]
readme/part/37/37part.FCStd
150.0 x 40.0 x 15.0 mm

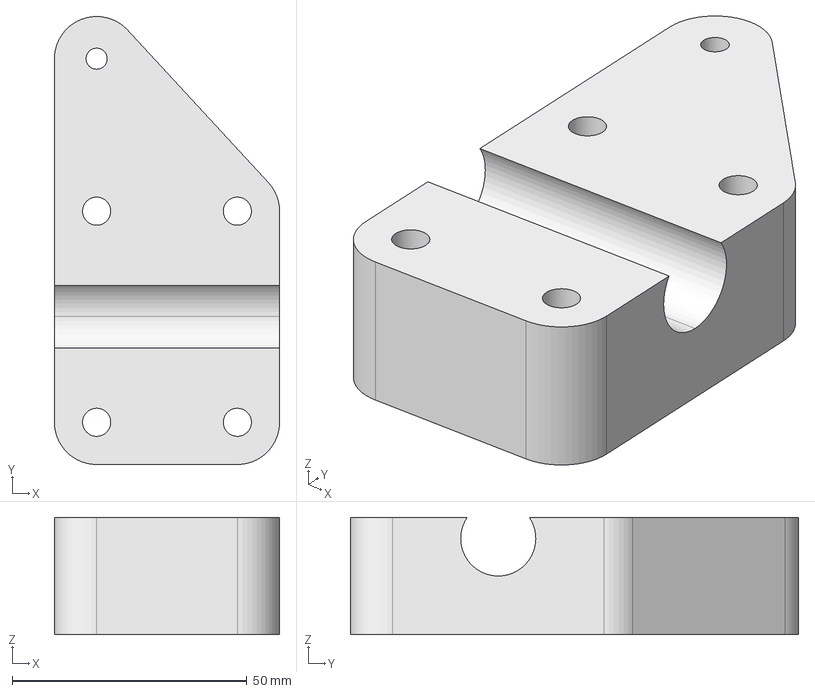
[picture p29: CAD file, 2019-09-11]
readme/part/52/52part.FCStd
48.0 x 95.5 x 25.0 mm

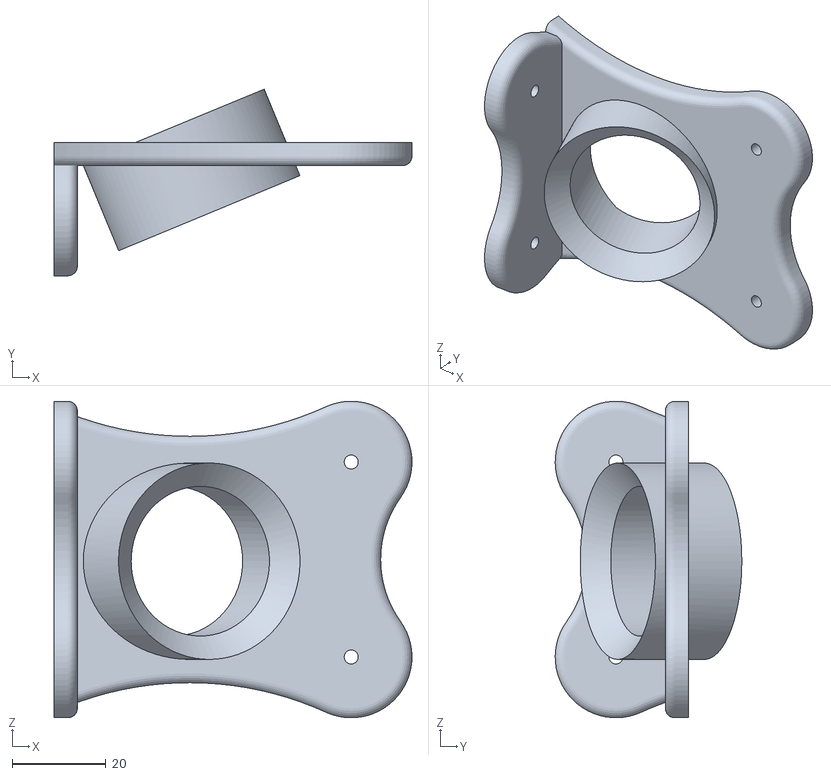
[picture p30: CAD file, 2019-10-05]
readme/part/54/54part.stl
76.6 x 39.9 x 67.7

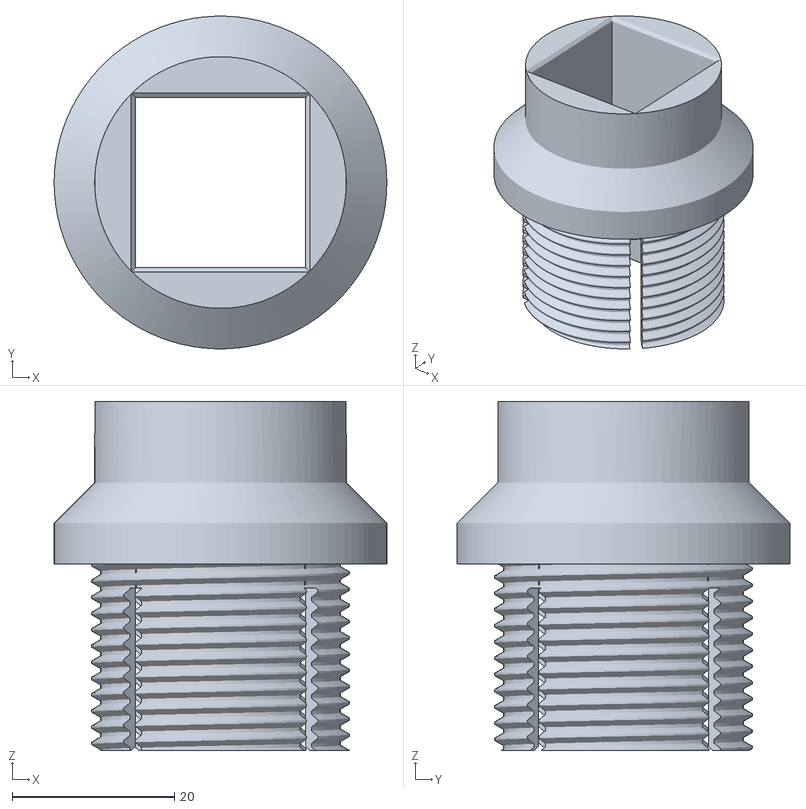
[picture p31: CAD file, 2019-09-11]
readme/part/55/55part.stl
41.0 x 41.0 x 43.0

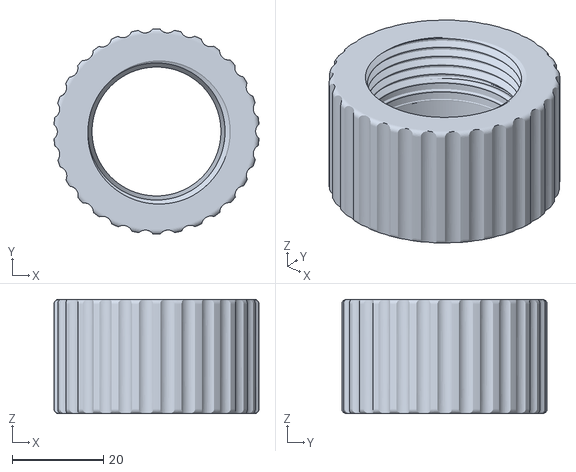
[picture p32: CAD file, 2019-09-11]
readme/part/56/56part.stl
44.9 x 45.0 x 25.0

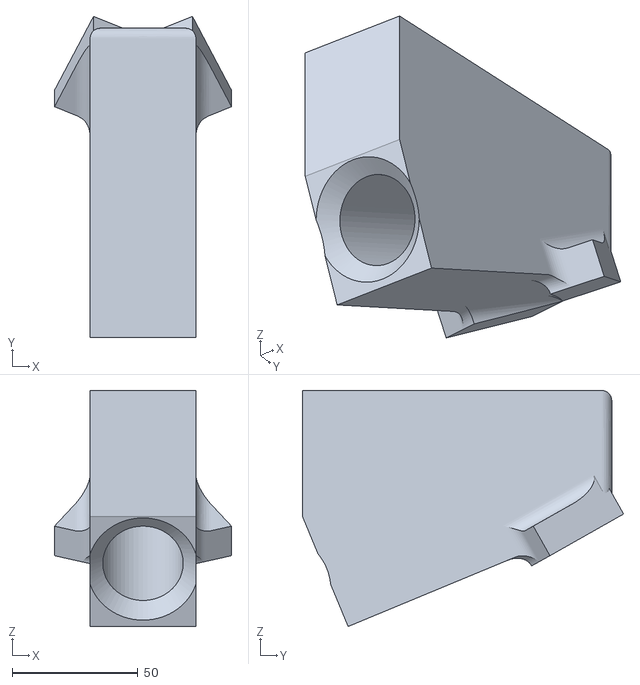
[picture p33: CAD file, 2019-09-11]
readme/part/57/57part.stl
70.4 x 127.7 x 93.8

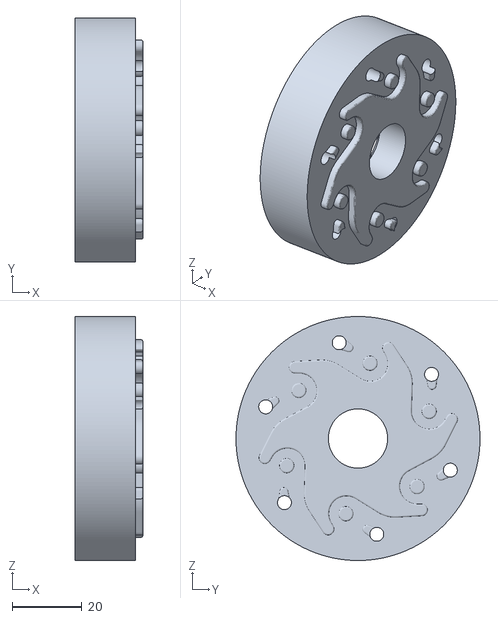
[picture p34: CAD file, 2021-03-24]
readme/part/71/71part.stl
19.5 x 70.0 x 70.0

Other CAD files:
readme/akkerman01.f3d
readme/akkerman02.f3d
readme/part/01/01part.f3d
readme/part/02/02part.f3d
readme/part/03/03part.f3d
readme/part/04/04part.f3d
readme/part/05/05part.f3d
readme/part/06/06part.f3d
readme/part/07/07part.f3d
readme/part/08/08part.f3d
readme/part/09/09part.f3d
readme/part/10/10part.f3d
readme/part/11/11part.f3d
readme/part/12/12part.f3d
readme/part/13/13part.f3d
readme/part/14/14part.f3d
readme/part/15/15part.f3d
readme/part/16/16part.f3d
readme/part/17/17part.f3d
readme/part/18/18part.f3d
readme/part/19/19part.f3d
readme/part/20/20part.f3d
readme/part/21/21part.f3d
readme/part/22/22part.f3d
readme/part/23/23part.f3d
readme/part/24/24part.f3d
readme/part/27/27part.f3d
readme/part/29/29part.f3d
readme/part/30/30part.f3d
readme/part/32/32part.f3d
readme/part/34/34part.f3d
readme/part/35/35part.f3d
readme/part/36/36part.f3d
readme/part/37/37part.f3d
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

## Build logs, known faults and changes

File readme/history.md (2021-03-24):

### История возникновения
У ребенка имелся гироскутер который через 1,5 года сломался (сдох аккумулятор), 
а так как считаю, гироскутер не практичной вещью, задумал пустить его на запчасти или сделать что-нибудь полезное.

Первая мысль - электросамокат (на мой взгляд куда более практичная вещь) изучив подобные переделки (электросамокат из гироскутера), 
пришло понимание, что самокат из таких запчастей тот еще монстр.
Основной недостаток конечно колеса 10 дюймов и длинная ось для крепления в одну сторону, 
еще немаловажный недостаток массивная тяжелая рама (к 13 кг гироскутера как минимум килограмм 5).
В итоге гораздо крупнее собратьев, не говоря об эстетической составляющей, было принято решение о не целесообразности такого изделия.
Бродя просторами интернета наткнулся на продажу новых гироскутеров, цена приятно удивила, почти в 2 раза дешевле за туже модель,
при этом получаем еще 2 колеса контроллер для них и аккумулятор.  
И родилась идея что можно монстра сделать на 4 колесах - электро карт с полным приводом. 
Отсутствие гаража наложило на конструкцию будущего изделия ограничения по габаритам, пройти в дверь, влезть в лифт.
 
Первым этапом стало создание [3d модели](scooter4ewd001.max)

Взяв проекцию как [сидит человек в обычной машине](https://www.google.com/search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), 
начал набрасывать расположение основных элементов. 
За основу строительного материала была взята металлическая труба 1/2 дюйма.
Конструкция обзавелась задней осью, передней осью, рамой, рулем. 
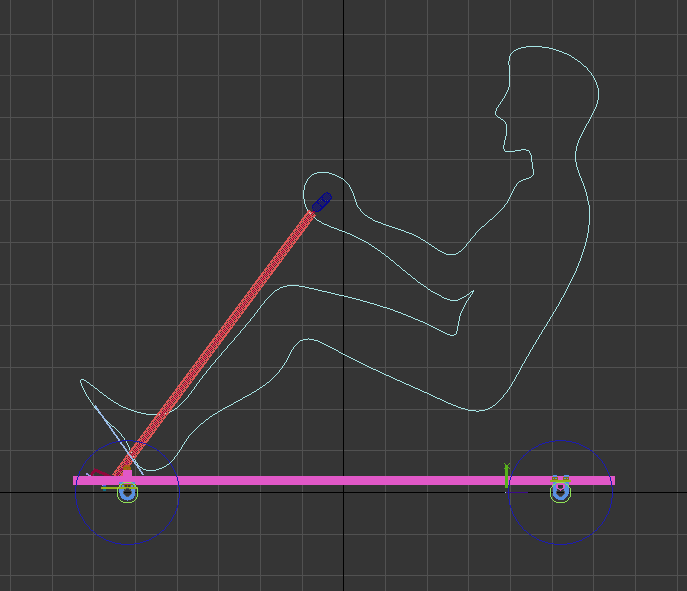
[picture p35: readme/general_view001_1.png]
Вид с боку

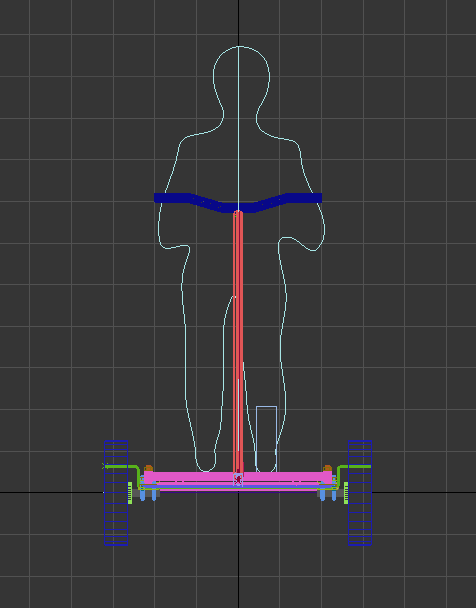
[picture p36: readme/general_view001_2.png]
Вид с переди

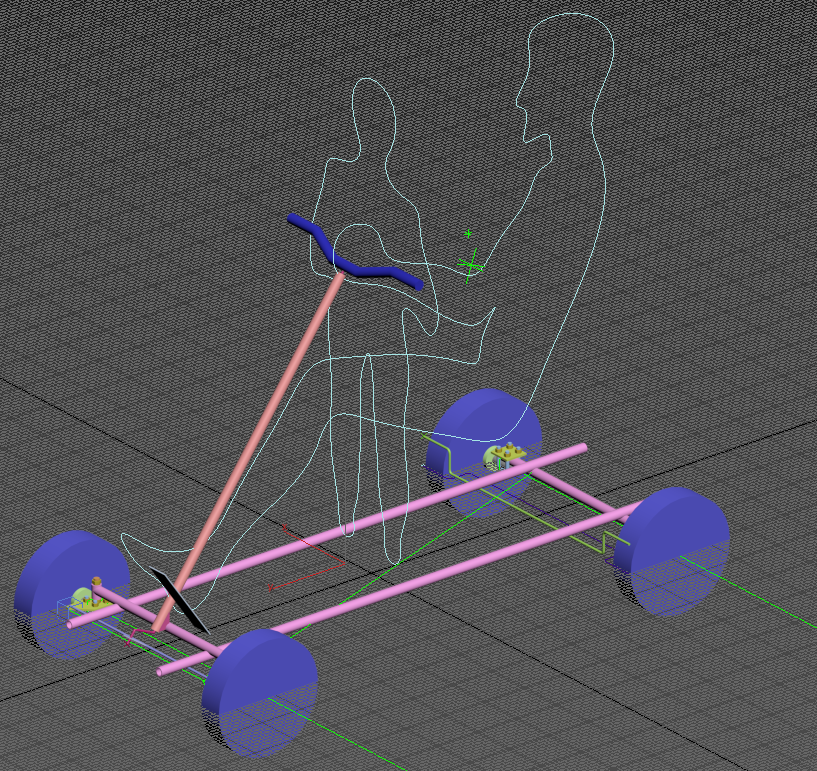
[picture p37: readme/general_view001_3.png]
Общий вид

В 3D удобно проверить угол поворота колес, взаимодействие элементов конструкции, 
но нужно было решение простое в исполнении, так как то, что легко сделать в 3D, могло сильно усложнить реализацию. 
Так некоторые решения после моделирования были откинуты с мыслями для изготовления этой детали понадобится токарный, 
а то и фрезерный станок.
В результате самый сложный узел - рулевое управление, решил использовать цельную рулевую рейку сопряженную через петлю с осью руля.
Про "угла Аккермана" натыкался на видео в интернете, его заложил в конструкцию, но проверка на 3D модели выявила некоторые неточности,
описание которым так и не удалось найти в интернете,
длина рычагов, конструкция трапеции наверное накладывает свои корректировки, как результат цент задней оси был смещен во внутрь, 
что позволило добиться оптимального положения при максимальном вывороте, и неплохо на промежуточных углах, 
в идеале вопрос требует изучения, но для полу детской машинки решил оставить так.    

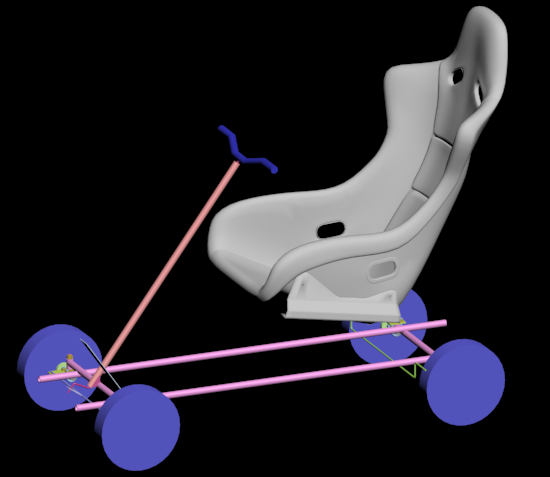
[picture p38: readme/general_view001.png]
Первая версия

Имея на руках виртуальную раму захотелось сделать корпус, перебрав кучу материала, наиболее понравился, Mercedes-Benz Bionic, 
в результате получилась 
[3d модель](mercedes%20bionic.max)

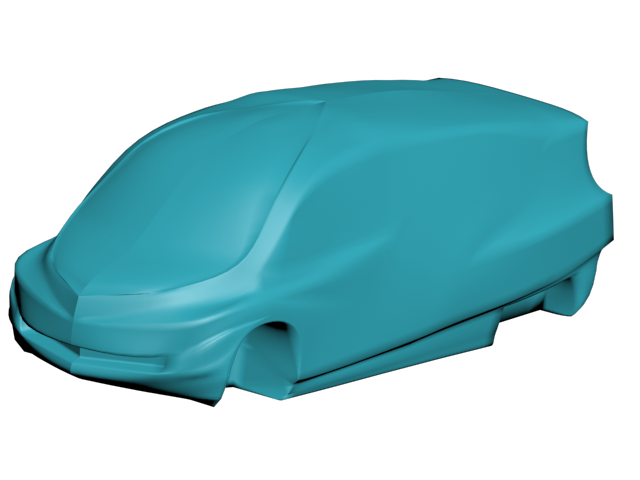
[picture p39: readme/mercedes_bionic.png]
Mercedes Bionic


А вот подружить две 3d модели не получилось нужно сильно укоротить и поднять, получился монстр. 

Хотелось попробовать в живую, проверять общую концепцию (влезет ли человек, зубы коленками не выбьет :-) ). 
Первый прототип был сделан из опилок (ДСП), вроде как нормально получилось в плане геометрии. 
Конечно, прототип не двигался, хрупкий материал требовал подпорок в нагруженных местах и со временем части начали разваливаться.

Хотелось собрать работающий прототип, но браться за сварочный не позволяли условия (отсутствие гаража), 
покопавшись в закромах были найдены деревянные брусья, пластмассовый стул.
Адаптировал [3d модель](scooter4ewd003.max) к новым материалам и строительство началось из них.

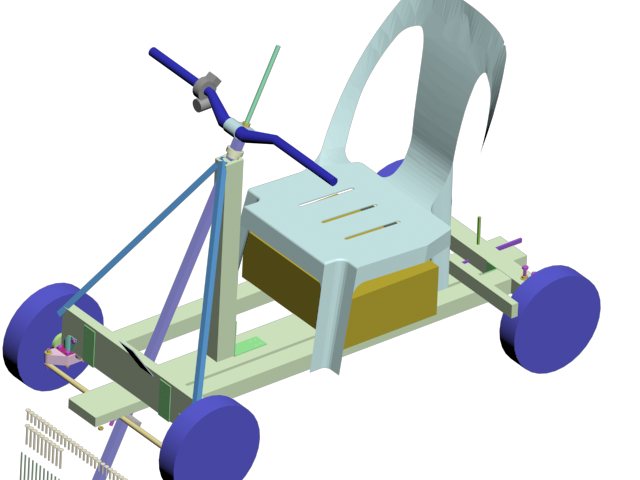
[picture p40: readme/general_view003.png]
Версия из брусьев
 
 
Собрав раму было решено, что стоит двигаться дальше - куплен второй гироскутер.
Здесь как в поговорке "скупой платит дважды", дешёвый гироскутер не работал, без предупреждения отключался и хватало его от силы на 10 минут.
Три раза меняли аккумулятор, каждый раз приходилось ездить в магазин, полностью заряжать, кататься пока не отключится. 
Последний вроде ничего, по крайней мере гироскутер предупреждал что садится.
Минусы на этом не закончились, сам гироскутер отличался от старого, особенно расстраивало наполовину пластмассовые колеса,
ранее они были полностью алюминиевые.
Как я узнал позже на собранном авто с подключенным ваттметром, мощность далека от заявленной, 
оба гироскутера позиционировали себя как 700вт (350вт на колесо),
замер же показал что старый 200Вт на колесо, новый 150Вт на колесо и довольно быстро начинает греться. 
Но на тот момент я об этом не знал, а был расстроен фактом что плата управления кардинально отличалась от описанной в [интернете](https://github.com/NiklasFauth/hoverboard-firmware-hack).
Изначально планировал использовать родной контроллер от гироскутера, но подружится с ним у меня не получилось,  
задумка перепрошить их была окончательно убита когда в ходе экспериментов по не осторожности статикой убил один из контроллеров. 
Плюнул и заказал на китайском сайте сразу ЧЕТЫРЕ контролера на электровелосипед для каждого колеса по 350вт каждый (что добавило 2 500 руб :-( ). 

Перешел к механике. Имея все 4 колеса столкнулся с проблемой как приделать их к раме да так чтобы еще поворачивать,
день рассматривания имеющихся деталей в строительном магазине завершился покупкой мебельных колес [№20](part/20/20part.md).
Плоская часть, площадка с отверстиями крепилась к оси колеса гироскутера [№1](part/01/01part.md), 
прижималась, выпиленной из бруса деталью, являющейся одновременно поворотным рычагом.
само колесико вынималось, а вилка обхватывало раму 

Рама стоит на 4 колесах, один контроллер был прикручен к доске та на петлях к раме, 
доску можно было наклонять и так машина самостоятельно смогла ездить (вперед/назад), но детишкам и этого было достаточно, 
без аварий не обошлось, специфика управления, а именно отпустив рычаг, платформа накланялась и контроллер давал полный газ вперед,
в результате следы покрышек на полу и сломанное крепление переднего колеса.

Сломанная деталь [№52](part/52/52part.md) напечатана за 3d принтере, доделано рулевое управление, 
понадобилась еще одна напечатанная деталь [№37](part/37/37part.md), конструкция поворачивает, дети продолжают кататься

Расматривая вариант возможности готовое изделие оставлять на улице все самое ценное с него должно быть съемным 
(чемоданчик с аккумуляторами и контролером),
ставится под сидение и подключается отключается, тут меня ждала суровая реальность 4 колеса от каждого 3 силовых провода 
и 5 проводов на датчики хола, общее питание конечно можно обединить, но итоговая цифра меньше не становилась, 
плюс провода управления. Вопрос звучал так "чем можно подключить 33 провода часть из которых силовые", 
в голове всплывали воспоменания о пром оборудовании и красивых мощных надежных раземах времен CCCP, 
но поиски не дали результата или ценник мягко говоря смущал, выбор остановил на разъеме похожий на компьютерный com порта только с 78 контактами.
И тут очередная суровая реальность припоять 176 проводка (2 разьема по 78 + 4 датчика хола по 5), 
что тут только небыло и осознание что паять не умею и оправдания паяльник не такой. 
С горем по полам распоял по составленой зарание [табличке](part/39/39part.md) все провода, здесь как уже упоменал в примечаниях я допустил ошибку,
что не стал припаивать провода к не задействованым пинам. 
Припаять 2 проводка для включения заднего хода на собранной машине стала грандиозной задачей.  

Пока идут детали решил заняться корпусом. С 3d не получилось, пробую в физическом мире, теперь за прототип взят милый автомобиль от гугла,
итоговый корпус планируется из стекловолокна, но надо с чего-то начинать - картон и ПВА. Легко резать, материала много, 
не жалко переделать, да и огрехи легко устранять, из минусов долго сохнет.
Весь корпус разделил: задний бампер, порог с частью пола (левый и правый), нос, верхняя часть кузова съемная, 2 двери. 
Лобовое стекло думал взять готовое, по городу катаются трехколесные скутеры развозки пиццы и по идеи товар ходовой, но цена в 9000 руб. остановила,
когда дойдет дело куплю лист прозрачного поликарбоната из минусов изгиб только в одно направление.

Ремарка: в процессе обклейки приходилось ворочать раму и даже в деревянном исполнении это > 25 кг, большую часть из которых составляет колеса,
так что на этом этапе есть четкое понимание что делать из стальных труб сделает машинку не транспортабельной, 
как вариант тонкая скилетная структура или алюминиевый профиль, 
ну или если работа со стекловолокном окажется не сложной можно попробовать из композитного материала, ну а, что помечтать то можно.

Контролеры пришли, в одной посылке, но все разные, разбираю и понимаю что это отремонтированные экземпляры, но делать нечего, 
проверяю, все работают. Прячем это все в чемодан, такого количества проводом я явно не ожидал, 
<!-- TODO -->
хорошо, что до включения питания решил прозвонить все провода, как в итоге 1 обрыв (при зачистке витой пары порвал жилу под оплеткой), 
1 замыкание (силовые провода, припаивая к пинам разъема делил на 4 и припаивал соответственно к четырем пинам и иногда объединял их оловом,
и от одного такого наплыва олово припаялось к соседней ноге, но другого провода). Убить транзисторы или еще чего не составит труда.

Выявленные проблемы:
Все четыре колеса работают, одно ведет себя странно, стартует раньше всех рывком, проверял, проверял, оказалось один датчик хола накрылся,
как результат контролер переходит в режим без датчиков хола. 
Плохо зажатый провод приводил к полной остановке машины после кочки.
Очень слабая тяга, если детям хватало, то мою тушку в 90кг на небольшом наклоне достаточно чтобы остановиться.
Тут оказалось питание на датчик хола ручки газа был занижено, взял 5 вольт с другого контроллера стало лучше.
Еще неприятная особенность контроллеров на велосипед, в отличии от гироскутера где режим удержания норма эти должны вращаться 
и если этого не происходит даже при малом токе контроллер вырубается, горку надо преодолевать на газу.

Не хватало заднего хода, провода для него нет, но так как плата контроллера видать была разработана как универсальная и как можно более функциональней, 
на ней есть контакт на который достаточно подать землю и мотор будет вращаться в реверсивном режиме. 
Припаять к платам контролера не составило труда, а вот добавить его на разъем очень сложно, когда уже все собрано.

Аккумуляторы работали в паре (параллельно) и их хватало на 30 минут катания ребенка, приобретённый ваттметр показал, 
что колеса совсем слабые в пике 700вт 25A.  

Из механических проблем больше всего доставлял руль, использование шпильки м10 как оси руля давало люфт градусов 30, 
торсионное скручивание было настолько ощутимо и не требовало больших усилий, даже та разность что одно колесо включалось раньше соседа 
поворачивало колеса при этом руль оставался неподвижен.

Шпильку заменил на алюминиевую трубу квадратного сечения, что потребовало немалых переделок в конструкции, 
так как детали напечатанные на 3D принтере показали себя хорошо, рулевое управление было во много сделано из напечатанных деталей.

Добавил тормоз, педаль тянула трос, который через блок прижимал к колесам брус. Испытания показали, что тормоза слабые, 
максимум, что удалось придумать это добавить еще один блок, что увеличит силу в 2 раза.

В таком состоянии катаемся, поломки по мелочам случаются, но в принципе эксплуатация нормально, 
докупил еще 2 аккумулятора от гироскутера, 
перепробовал несколько магазинов, но везде они далеки от заявленных 4.4 Ah, наилучшее что нашел 2.2 Ah. 
Теперь машинка проезжает 60 минут или 25 км. 
Начал делать электронный тормоз, на контроллере есть для этого контакты, припаял провод, 
замкнув его с землей контролер отключается, это поведение по умолчанию, но если замкнуть 2 контакта на контроллере то при торможении включает рекуперация.

Длительная поездка выявила основной недостаток конструкции - отсутствие подвески и какой либо амортизации.
Разбор конструкции и попытки добавить степеней свободы заканчивалось либо нет хода и конструкция такая же жесткая 
либо колеса начинали ходить во всех направлениях, более менее казалась идея второй рамы поверх первой с проставками, 
но колоссально увеличивались размеры, не оставалось места под чемодан, результата нет, собрал, как было.
Уходим в интернет, натыкаюсь на книгу "Книга самодеятельного конструктора автомобилей" рекомендую к прочтению.
Из неё взял макет [человека](man.max). 
Очень понравилась подвеска на торсионах, своей простотой и компактностью, подобная схема используется в дорогих электросамокатах, 
на первый взгляд система очень простая два квадрата большего и малого сечения помещённый внутрь первого со смещением на 45 градусов, 
а все свободное пространство заполнено эластичным элементом, пружина и амортизатор в одном.

Просматривая материалы, занесло в тематику постройку багги, какие вещи люде делают, можно только позавидовать, 
но насторожила фраза одного самодельщика что постройку надо начинать с поиск донора, так как целый автомобиль на порядок дешевле покупке запчастей,
цену за своего донора он озвучил в 15 000 рублей, я не поверил и полез в поиск б/у авто, у меня чуть челюсть не отвалилась,
оку на ходу с документами можно купить за 30 000 руб (цена на лето 2019 г.) что равно сумме вложенной в мою поделку на тот момент. 
Но желание сделать свое победило здравый смысл и переключился на создание виртуальную модель [v4](scooter4ewd004.max)  
v4. 

<!-- TODO Заказал гидравлические тормоза, когда пришли смоделировал проставку --> 

Угол Аккермана не давал покоя, сделал две модели:
  - Простая трапеция
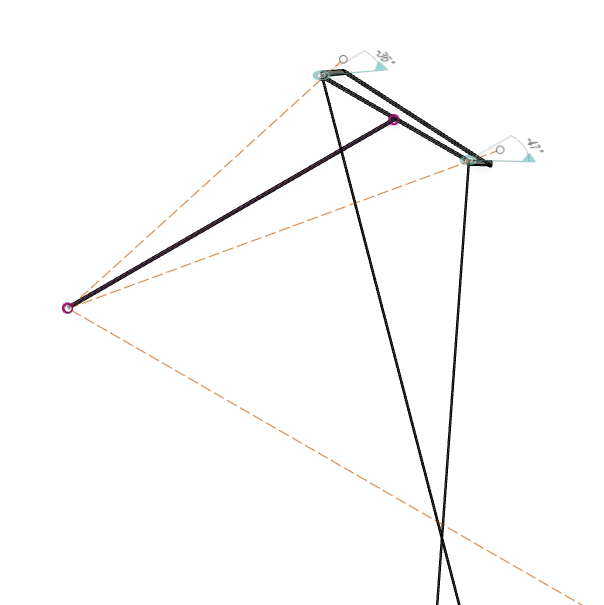
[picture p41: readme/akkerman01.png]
Простая трапеция
 
[3D модель](akkerman01.f3d)

Геометрия была оптимальна только для некоторого угла в остальных случаях все было плохо.
  - Схема применяемая в картинге
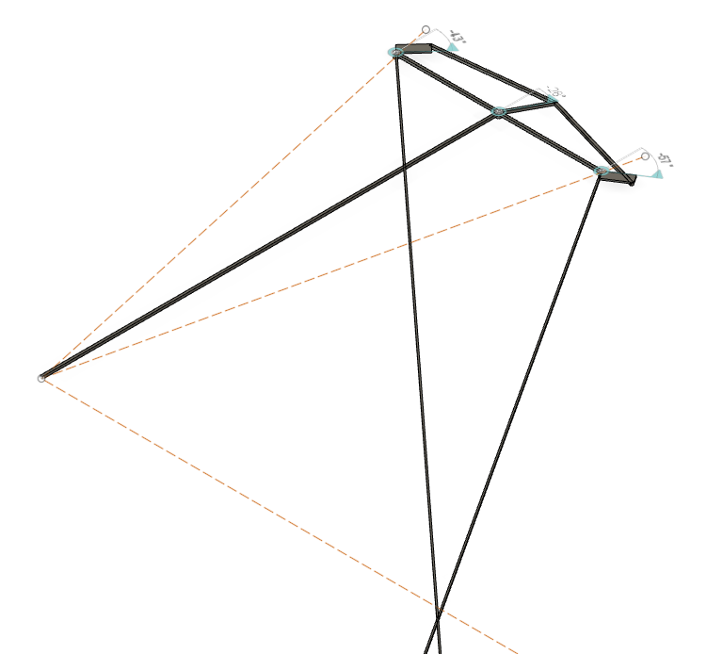
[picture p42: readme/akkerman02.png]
Схема применяемая в картинге
 
[3D модель](akkerman02.f3d)

Вторая схема оказалась лучше, но на геометрию сильно влияла длина поворотного кулака и длина рулевой сошки, 
не найдя ответа как их расчитывать, решил определить методом перебора. 
Написал [программу](../src/main/java/scooter4ewd/BruteForceAnkerman.java) 
которая перебирала значения и определяла оптимальные значения, перенеся полученные значения на 3d модель, 
точка пересечения осей передних колес была наиболее близка к задней оси, но всё равно не идеально.

Итоги
задумывался как дешевый, по факту > 30 000 руб, и это при попытках сэкономить на всем

TODO

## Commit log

2019-09-11 Описание scooter4ewd
    [01part.f3d, 02part.f3d, 03part.f3d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]
2019-10-05 Изучение угла Аккермана
    [29_1part.stl, 29_2part.stl, 29part.f3d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]
2019-10-13 Изучение угла Аккермана, разная конструкция трапеции
2020-03-07 Добавление 3d мадели: 39. Разем DHS-78
    [39_1part.f3d, 39_2part.f3d]
2020-03-07 Добавление отсутствующей картинки общего вида для первой версии
2021-03-24 График ошибки для BruteForceAkkerman10
2021-03-24 Актуализация списка использованных запчастей
    [01part.f3d, 02part.f3d, 03part.f3d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]
